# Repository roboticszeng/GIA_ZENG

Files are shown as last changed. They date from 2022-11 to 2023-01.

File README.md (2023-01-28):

# GIA_ZENG开发文档

| 更新时间  | 版本号 | 更新内容 | 负责人 |
| --- | --- | --- | --- |
| 2023.1.21 | V0.2 | 初始化文档 | RoboticsZeng |

## 1.结构设计

==Reserve==

## 2.硬件设计

==Reserve==

## 3.软件设计

GIA_ZENG软件层按照应用功能主要分为以下几部分：FOC控制、自标定、数据存储和对外通讯，其中包含相关驱动的开发和数值解算。下面分别详细说明。

### 3.1 FOC控制

FOC控制是BLDC驱动的核心功能，其流程如下图所示：

==缺一张网图==

上述功能主要依赖以下算法：SVPWM计算、位置速度估计、电流估计、PI控制器、滤波器。另外需要相应的硬件驱动开发。

#### 3.1.1 SVPWM计算

GIA_ZENG采用的是有感FOC，故电角度为已知量，首先进行反park变换：
$$
U_{\alpha} = U_d\cos q_e + U_q\sin q_e
$$

$$
U_{\beta}=U_d\sin q_e + U_q\cos q_e
$$

==Reserve==

#### 3.1.2 位置速度估计

AS5600可以直接获得12位绝对位置，通过单位转换函数`convert_pulse_to_angle`转换为角度，单位rad。

速度采用M法进行估计，如下式：
$$
v=(p-p_{prev})/T
$$
其中，$p$为当前时刻位置，单位rad；

$p_{prev}$为上一时刻位置，单位rad；

$T$为编码器采样时间，单位s；

$v$为估计速度值，单位rad/s。

#### 3.1.3 电流估计

INA240可以直接通过12位ADC获得两相电压值，进行校正后再通过单位转换函数`convert_pulse_to_current`转换为电流，单位A。进一步计算q轴和d轴的方式如下：

（1）Clarke变换到$I_{\alpha}, I_{\beta}$
$$
I_{\alpha}=I_a
$$

$$
I_{\beta} = \frac{\sqrt{3}}{3}(I_a+2I_b)
$$

（2）Park变换到$I_q,I_d$
$$
I_d=I_{\alpha}\cos q_e + I_{\beta}\sin q_e
$$

$$
I_q=-I_{\alpha}\sin q_e + I_{\beta}\cos q_e
$$

#### 3.1.3 PI控制器

本方案采用抗积分饱和的离散PID控制器，其逻辑如下：

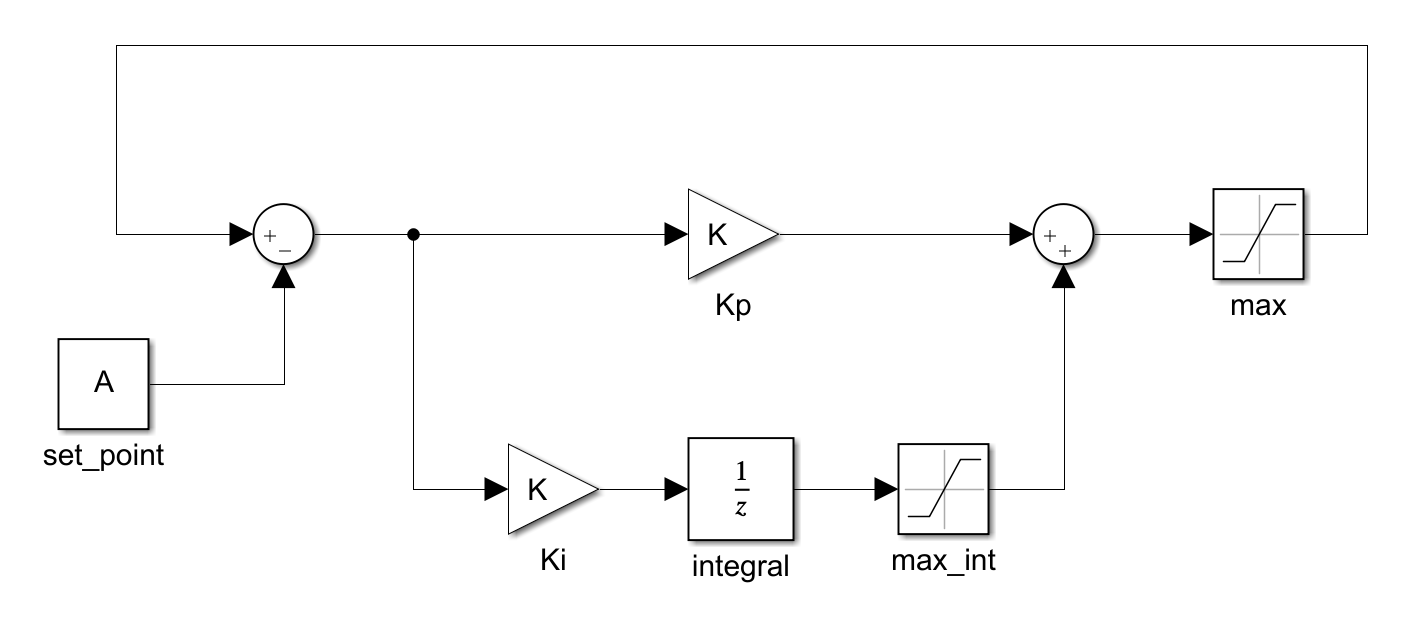
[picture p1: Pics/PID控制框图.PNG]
PID控制框图


PI控制器算法逻辑不再赘述。

#### 3.1.4 低通滤波器

本方案对速度、q轴电流和d轴电流计算时采用了一阶低通滤波器，其s域表达为：
$$
G(s) = \frac{1}{\frac{s}{2\pi f_c} + 1}
$$
其中，$f_c$为数字截止频率。

向后差分到z域再写成差分方程：
$$
y(n)=\frac{RC}{T_s+RC}y(n-1)+\frac{T_s}{T_s+RC}x(n)
$$
其中，$T_s$为采样时间，$RC=\frac{1}{2\pi f_c}$

#### ==3.1.5 展望==

- 加入数字截止频率到模拟截止频率的转换
- 改为二阶butterworth滤波器
- 向后差分改成tustin

### 3.2 电角度&ADC校正

本方案对电角度和ADC偏置量采用了自动和手动校正的方法，具体步骤如下：

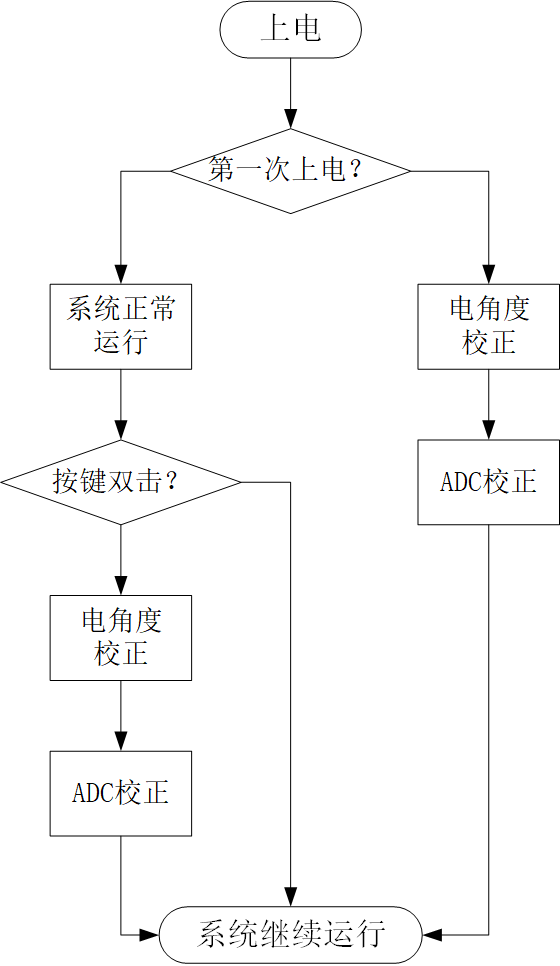
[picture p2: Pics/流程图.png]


#### 3.2.1 电角度校正

设置开环SVPWM控制如下：

| $U_q$ | $U_d$ | $q_e$ |
| ----- | ----- | ----- |
| 0.5 | 0.0 | 0.0 |

注意此处的$U_q,U_d$为相对供电电压的相对值，取值范围$[-1,1]$

循环设置N次上述电角度对正，同时通过编码器读取当前位置，求平均值得到校正的电角度，作为单位转换函数`compute_position_elec`的配置项。

#### 3.2.2 ADC校正

设置控制模式为MODE_NO确保驱动器未使能，当前电流为零，循环采集N次此时刻的ADC值，求平均值得到校正的ADC偏置量，在ADC采样时作为输入。注意由于INA240芯片易损坏，此处需要手动check偏置量是否正确，即观察偏置值是否在2048附近。

#### ==3.2.3 展望==

- 校正时需要加入合理的小灯闪烁来指示正在校正
- 加入ADC求偏置的单位转换函数，不要直接写在ADC采样内

### 3.3 CAN通讯

本方案当前仅采用了CAN通讯与其他MCU或上位机交互数据，同时USART用于打印调试信息。文档中仅介绍CAN通讯。CAN读写均采用扩展数据帧形式，数据形式定义为PDO（循环上报）和SDO（根据指令上报）。

#### 3.3.1 CAN读取

（1）PDO

PDO数据循环上报，无需读取，其数据格式为：

| data[0] | data[1] | data[2] | data[3] | data[4] | data[5] | data[6] | data[7] |
| --- | --- | --- | --- | --- | --- | --- | --- |
| mode_h  | mode_l  | actual_pos_h | actual_pos_l | actual_vel_h | actual_vel_l | actual_cur_h | actual_cur_l |

其中，\*\_h和\*\_l分别为*的高八位和低八位。其具体数值和单位转换的方式参考附录。

（2）SDO

读取数据格式为：

| data[0] | data[1] | data[2] | data[3] | data[4] | data[5] | data[6] | data[7] |
| --- | --- | --- | --- | --- | --- | --- | --- |
| 0x56 | id* | Reserve | Reserve | Reserve | Reserve | 0x0d**  | 0x0a |

*：id为当前关节的id号，默认为0x00

**：推荐的值，当前程序还没有设置check这一位

软件在收到数据头为0x56的CAN数据包后开始解析，将当前CAN地址下的SDO数据返回。

#### 3.3.2 CAN写入

PDO和SDO的写入逻辑相同，均是在软件内重构了CAN_RX中断，读取的数据格式为：

| data[0] | data[1] | data[2] | data[3] | data[4] | data[5] | data[6] | data[7] |
| --- | --- | --- | --- | --- | --- | --- | --- |
| 0x55 | id | data_h  | data_l  | Reserve | Reserve | 0x0d | 0x0a |

软件在收到数据头为0x55的CAN数据包后开始解析，将当前CAN地址下的PDO或SDO数据写入控制器。

#### 3.3.3 PDO/SDO转换

上位机向控制器发送PDO/SDO后，还需要将这一`uint16_t`类型的标准参数转换为实际使用的配置值或控制目标值，这一逻辑较复杂，具体分为以下几种情况：

（1）收到的数据是PDO：MODE_OF_OPERATION, TARGET_POSITION, TARGET_VELOCITY, TARGET_CURRENT

- STEP1: 解析地址，将收到的数据存入PDO结构体的指定成员中。
- STEP2: 由下式转化为State结构体的指定成员。

$$
State=256*PDO_h+PDO_l
$$

- STEP3: FOC三环控制的定时器中断中只调用State成员的变量进行实时控制，而不考虑PDO的问题

（2）收到的数据是除上述之外的PDO：无意义，不作响应

（3）收到的数据是SDO，但不是`SDO->ID`或`SDO->SAVE_FLASH`

- STEP1: 解析地址，将收到的数据存入`SDO->SDO_ID`
- STEP2: 调用函数`para_init`初始化所有config参数

`para_init`函数包括：

#### ==3.3.4 展望==

- CAN回传PDO时只用了一个邮箱传输了部分数据，这是由于邮箱容易被占用阻塞，后续应解决这一问题

### 3.4 配置读写和存储

配置读写和存储的逻辑较为复杂，具体的涉及到以下几个方面：CAN通讯收到的PDO/SDO数据转换为实际使用的配置值或控制目标值；上电时的配置读取逻辑；基于内部FLASH的数据存储逻辑。下面分别叙述。

#### 3.4.1 PDO/SDO的转换

#### 3.4.2 配置参数读取

#### 3.4.3 配置参数存储

### 3.5 依赖硬件的说明

本文档中对硬件驱动的详细逻辑不再赘述，仅给出依赖硬件驱动的说明。

STM32CUBEMX引脚总览：

| 引脚 | 名称 | 备注 |
| ---- | --- | --- |
| PA0  | ADC1_IN0  | |
| PA1  | ADC1_IN1  | |
| PA2  | USART2_TX | |
| PA3  | USART2_RX | |
| PA4  | SEN_DIR | 编码器方向定义 |
| PA5  | KEY | 按键输入，软件暂未实现 |
| PA8  | TIM1_CH1  | PWM-U相输出 |
| PA9  | TIM1_CH2  | PWM-V相输出 |
| PA10 | TIM1_CH3  | PWM-W相输出 |
| PA11 | CAN_RX | |
| PA12 | CAN_TX | |
| PB5  | SENS_OUT  | 编码器电压输出（当前版本不用） |
| PB6  | I2C1_SCL  | 编码器I2C通信 |
| PB7  | I2C1_SDA  | 编码器I2C通信 |
| PC13 | LED | |

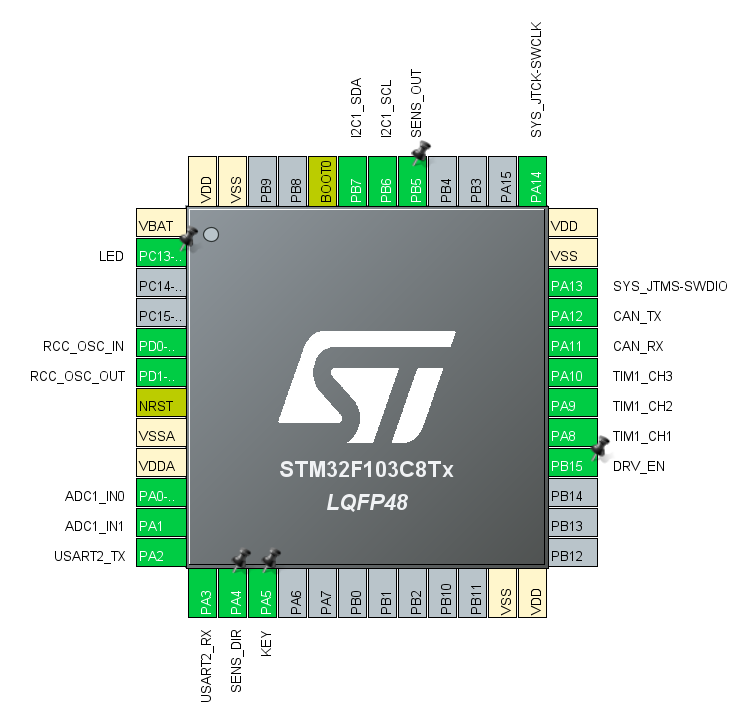
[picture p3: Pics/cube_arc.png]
cube_arc


#### 3.5.1 定时器中断

本方案中采用了四个定时器中断如下：

| 定时器 | 分频值PSC | 重装值ARR | 周期T | 频率f | 功能简介 |
| --- | --- | --- | --- | --- | --- |
| TIM1 | 2-1 | 1500-1 | 41.67us | 24kHz | 生成PWM波&电流采样&电流滤波 |
| TIM2 | 300-1 | 240-1 | 1ms | 1000Hz | 编码器采样&速度估计滤波&CAN上报 |
| TIM3 | 160-1 | 72-1 | 160us | 6.25kHz  | 计算SVPWM&电流环PI控制 |
| TIM4 | 160-1 | 144-1 | 320us | 3.125kHz | 位置环&速度环PI控制 |

注：定时器分频、重装值和周期/频率的转换关系如下：

公式：
$$
T=(ARR+1)*(PSC+1)/f_{ck}
$$

$$
f=\frac{1}{T}
$$

$f_{ck}$为主频，单位Hz。对于STM32F103C8T6，$f_{ck}=72\times10^6$Hz；$T$单位为s。

#### 3.5.2 I2C通讯

编码器AS5600通过I2C与主控制器通信，模式Fast Mode，通信速率400kHz

#### 3.5.3 ADC读取

主控制器通过ADC1双通道IN0和IN1读取两片INA240的电压，采用DMA方式。

#### 3.5.4 按键外部中断

设置PA5引脚为GPIO_EXTI5，EXTI_line[9:5] interrupt中断优先级5，注意此处必须设置System Ticker Timer优先级小于5，否则可能会在中断处卡住。

本方案对按键中断设计了单击、双击、长按三个事件，其功能如下：

| 事件 | 功能 |
| --- | --- |
| 单击 | 指示灯电平翻转 |
| 双击 | 手动电角度&ADC校正  |
| 长按（>1s） | 存储数据到内部FLASH |

#### 3.5.5 CAN通讯

#### 3.5.6 内部FLASH

## 4.附录

### 4.1 单位转换

### 4.2 通讯协议详解

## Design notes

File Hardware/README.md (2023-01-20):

# GIA硬件板卡设计

## 1.总览

### 1.1 IC及原理图设计

- STM32F103C8T6：

最小板参考已实现的方式设计，不要低频晶振

- L6234PD（补购10片）

参考已实现的方式设计，EN预留IO，注意务必理解、实现保护地和地

- AS5600

STM32预留可编程电阻和方向口的IO

- INA240A2*2（补购10片）

用嘉立创的0.01R电阻

- TPS54331（补购10片）

复用灯哥开源的电路

- ASM1117-3.3

参考验证版的选型和电路

- TJA1040T

预留120R终端电阻接口，但是不焊（调试时用上位机的终端电阻）(**明天开始先调CAN和flash算了。。。。**)

- 其他

LED灯查下匹配的电阻，不要太亮也不要太暗

### 1.2 接口（全部放在反面）

- [x] UVW：2.54-3P螺钉式接线端子
- [x] DCBUS：2.54-2P插拔式接线端子弯插
- [x] CAN***2**：SH1.0-2P贴片 / PH2.0-2P弯插
- [x] I2C：预留一路SH1.0-4P贴片（注意若SWD为SH1.0，务必保证和SWD的VCC/GND一致）
- [x] USART：SH1.0-3P贴片 / PH2.0-3P弯插
- [x] SWD：SH1.0-4P贴片 / PH2.0-4P弯插
- [x] LED：电源灯（蓝灯）、PC13灯（DEBUG绿灯）、编码器方向灯（红灯常灭）三个灯PCB上尽量放在一起
- [ ] INA240-IO引脚留出，手焊短接，尽量方便手焊的位置
- [ ] PC13在边缘留一个焊盘用于DEBUG
- [ ] 留圆盘小按键用于重置STM32

### 1.3 PCB Layout注意事项

- [ ] 晶振不要放在边缘
- [ ] AS5600居中
- [ ] UVW端子观察电机布置
- [ ] 所有接口都贴在反面
- [ ] INA240贴在反面
- [ ] 灯都贴在反面
- [ ] 某两个孔中间角度连电机端子，依次均布接口不要超过电机端子的正负90deg
- [ ] 以后可以把编码器和控制器分开做异形PCB，想想都很酷炫
- [ ] PCB板直径68，孔距44，4个孔，思考下以后怎么安装

### 1.4 原理图设计注意事项

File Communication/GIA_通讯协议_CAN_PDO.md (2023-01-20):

# GIA\_通讯协议\_CAN_PDO

8位数据，数据头55，数据尾0d0a

## Bit[0]: 数据头0x55

## Bit[1]: 关节号Joint Number

| 取值 | 说明 |
| ---- | --- |
| 0xd0 | 关节1 |
| 0xd1 | 关节2 |
| 0xd2 | 关节3 |
| 0xd3 | 关节4 |
| 0xd4 | 关节5 |
| 0xd5 | 关节6 |
| 0xd6 | 关节7 |
| else | Error, returnBit[0] = 1 |

## Bit[2~3]: PDO值

### 1. ActualPosition==(ADDRESS = 0x3082)==

```
Bit[2] = _get_high_byte_uint(oPdo->actual_position)
Bit[3] = _get_low_byte_uint(oPdo->actual_position)
```

actual_position 取值范围 0~4096，直接由函数`as5600_get_raw_angle(oEncoder, &actual_position)`采集得到
$$
q=(p-p_0)\frac{2\pi}{4096}
$$

$$
p=\frac{4096}{2\pi}q+p_0
$$

==未实现的：==

```
#define _get_high_byte_uint(data) (data & 0xff00) //取无符号整型数据的高8位
#define _get_low_byte_uint(data) (data & 0x00ff) //取无符号整型数据的低8位
```

### 2. ActualVelocity==(ADDRESS = 0x3085)==

```
Bit[2] = _get_high_byte_int(oPdo->actual_velocity)
Bit[3] = _get_low_byte_int(oPdo->actual_velocity)
```

actual_velocity取值范围±20480（电机额定转速300rpm），由函数`get_velocity`计算得到
$$
\dot q=(p-32768)\frac{2\pi}{4096}
$$

$$
p=\frac{4096}{2\pi}q+32768
$$

==未实现的：==

```
#define _get_high_byte_int(data) ((data + 0x8000) & 0xff00)
#define _get_low_byte_int(data) ((data + 0x8000) & 0x00ff)
```

==未实现的：==

```
get_velocity 
```

### 3. Actual Current-Q==(ADDRESS = 0x330E)==

```
Bit[2] = _get_high_byte_uint(oPdo->actual_current_q)
Bit[3] = _get_low_byte_uint(oPdo->actual_current_q)
```

actual_current_q 取值范围0~4096，由函数`convert_current_to_pulse`计算得到

计算方法，已知电流采样时：
$$
I=\frac{p-2048}{K*R}*\frac{3.3}{4096}
$$
那么交换顺序：
$$
p=K*R*I*\frac{4096}{3.3}+2048
$$
其中，$K$为放大系数50，$R$为采样电阻0.01Ω，4096为ADC分辨率

==未实现的：==

```
convert_current_to_pulse
```

### 4. Actual Current-D==(ADDRESS = 0x330D)==

```
Bit[2] = _get_high_byte_uint(oPdo->actual_current_d)
Bit[3] = _get_low_byte_uint(oPdo->actual_current_d)
```

和3.完全一样

### 5. Mode Of Operation Display==(ADDRESS=0x3081)==

```
Bit[2] = 0x00;
Bit[3] = oPdo->mode;
```

mode取值范围0x00,0x08,0x09,0x0a

### 6. Following Error==(ADDRESS=0x3084)==

```
switch (oPdo->mode){
	case MODE_CSP:
	oPdo->following_error = oPdo->target_position - oPdo->actual_position;
	
	break;
	case MODE_CSV:
	oPdo->following_error = oPdo->target_velocity - oPdo->actual_position;
	
	break;
	case MODE_CST:
	oPdo->following_error = oPdo->target_current_q - oPdo->actual_current_q;
	
	break;
	otherwise:
	oPdo->following_error = 0;
	break;
}
// 上面的计算也可以放在三环里算

Bit[2] = _get_high_byte_int(oPdo->following_error)
Bit[3] = _get_low_byte_int(oPdo->following_error)
```

## Bit[4]~Bit[5]: 目标值TargetValue = Bit[4] * 0x100 + Bit[5]

### 1. Bit[2] == 0x08||0x09||0x0a

| Bit[2] Value | Bit[4] 含义  | 单位 | 取值范围 | 转换关系 |
| --- | --- | --- | --- | --- |
| 0x08 | 目标位置 | count | 0~4096 | TargetPos = Bit[2] |
| 0x09 | 目标速度 | count/s | 0~40960 | TargetVel = Bit[2] - 20480 |
| 0x0a | 目标电流 | count_i | 0~4096 | TargetCur = Bit[2] - 2048  |
| 0x08\|\|0x09\|\|0x0a | 超出取值范围 | | returnBit[2]=1 | |

示例：

Bit[2] = 0x08, TargetValue = 2048 ==> 目标位置为2048count

Bit[2] = 0x09, TargetValue  = 0 ==> 目标速度为-20480rad/s

Bit[2] = 0x0a, TargetValue  = 0 ==> 目标电流为-2048count_i

提供两个常数：

Const_count_to_pos = (2*PI)/4096 rad/count

Const_count_to_cur = 6.6/4096 A/count (INA240A2_50V/V + 0.01R)

### 2. Bit[2] == 0x10 || 0x20

上报16Bit配置参数，上报数据根据TargetValue的取值不同，输出格式如下

| Target Value | 数据位 | 说明 | 单位 | 取值范围 |
| --- | --- | --- | --- | --- |
| / | 0 | 数据头:0x55 | | |
| | 1 | Joint Number:0xd0~0xd6 | | |
| 0x3000:Actual State | 2.3 | Actual Position | | |
| | 4.5 | Actual Velocity | | |
| | 6.7 | Actual Current-Q | | |
| | 8.9 | Actual Current-D | | |
| | 10.11  | Mode of Operation Display | Next Ver | |
| | 12.13  | Following Error | Next Ver | |
| 0x3080:Target State | 2.3 | 最近一次Target Position | | |
| | 4.5 | 最近一次Target Velocity | | |
| | 6.7 | 最近一次Target Current-Q  | | |
| | 8.9 | 最近一次Velocity Offset | Next Ver | |
| | 10.11  | 最近一次Current Offset | Next Ver | |
| | 12.13  | 最近一次Mode Of Operation | Next Ver | |
| 0x3300:Pos Demand | 2.3 | Position Demand Value | | |
| | 4.5 | Limited Position | | |
| | 6.7 | Position Loop Effort | Next Ver | |
| 0x3303:Vel Demand | 2.3 | Velocity Demand Value | | |
| | 4.5 | Limited Velocity | | |
| | 6.7 | Velocity Loop Effort | Next Ver | |
| 0x3309:Cur-Phase Actual | 2.3 | Actual Current A-Phase | | |
| | 4.5 | Actual Current B-Phase | | |
| 0x330d:Cur-Q Demand | 2.3 | Current-Q Demand Value | | |
| | 4.5 | Limited Current-D | | |
| | 6.7 | Current-Q Loop Effort | Next Ver | |
| 0x330e:Cur-D Demand | 2.3 | Current-D Demand Value | Next Ver | |
| | 4.5 | \ | | |
| | 6.7 | Current-D Loop Effort | | |
| **0x3506:Pos Loop Para Std** | 6.7 | KP_P_STD | Next Ver | |
| | 8.9 | KI_P_STD | | |
| | 10.11  | KD_P_STD | | |
| **0x3507:Vel Loop Para Std** | 6.7 | KP_V_STD | Next Ver | |
| | 8.9 | KI_V_STD | | |
| | 10.11  | KD_V_STD | | |
| **0x3508:Cur-Q Loop Para Std** | 6.7 | KP_Q_STD | Next Ver | |
| | 8.9 | KI_Q_STD | | |
| | 10.11  | KD_Q_STD | | |
| **0x3509:Cur-D Loop Para Std** | 6.7 | KP_D_STD | Next Ver | |
| | 8.9 | KI_D_STD | | |
| | 10.11  | KD_D_STD | | |
| **0x3516:Pos Loop Para Per** | 6.7 | KP_P_PER | 0~65535  | 0.001 |
| | 8.9 | KI_P_PER | | |
| | 10.11  | KD_P_PER | | |
| **0x3517:Vel Loop Para Per** | 6.7 | KP_V_PER | | |
| | 8.9 | KI_V_PER | | |
| | 10.11  | KD_V_PER | | |
| **0x3518:Cur-Q Loop Para Per** | 6.7 | KP_Q_PER | | |
| | 8.9 | KI_Q_PER | | |
| | 10.11  | KD_Q_PER | | |
| **0x3519:Cur-D Loop Para Per** | 6.7 | KP_D_PER | | |
| | 8.9 | KI_D_PER | | |
| | 10.11  | KD_D_PER | | |
| **0x3510:Pos Limit** | 6.7 | 位置环上限幅 | count | |
| | 8.9 | 位置环下限幅 | count | |
| **0x3512:Vel Limit** | 6.7 | 速度环上限幅 | count/s  | |
| | 8.9 | 速度环下限幅 | count/s  | 上限取反 |
| **0x3514:Cur-Q Limit** | 6.7 | 电流环d轴上限幅 | count_i  | |
| | 8.9 | 电流环d轴下限幅 | count_i  | 上限取反 |
| **0x3515:Cur-D Limit** | 6.7 | 电流环q轴上限幅 | count_i  | |
| | 8.9 | 电流环q轴下限幅 | count_i  | 上限取反 |
| **0x3500:Motor Const** | 6.7 | 极对数：14 | | |
| | 8.9 | 供电电压：24 | V | |
| **0x3501:Encoder Const** | 6.7 | 线数：4096 | | 0~65535 |
| | 8.9 | 编码器偏置 | | Next Ver |
| | 10.11  | 电角度偏置 | | 待完成 |
| **0x3502:ADC Const** | 6.7 | 线数：4096 | | 0~65535 |
| | 8.9 | ADC_0偏置 | count_i  | -2048~2048 |
| | 10.11  | ADC_1偏置 | count_i  | -2048~2048 |
| **0x3503:Mechanical Const** | 6.7 | 电流和位置的方向：0(neg)  | | 0~1 |
| **0x3505:Cur-Sample Const** | 6.7 | 采样电阻：10 | mΩ | 0~65535 |
| | 8.9 | 增益系数：50 | V/V | 0~65535 |
| | 10.11  | MCU电压：3300 | mV | 0~65535 |
| / | 14 | 数据尾:0x0d | | |
| / | 15 | 数据尾:0x0a | | |

若Bit[2] = 0x20，则为写入模式，其取值同上表，只取到**加粗**的数值。

示例：

Bit[2] = 0x10, TargetValue = 0x3502：读ADC常数，按上表格式输出

Bit[2] = 0x20, TargetValue = 0x3502：写ADC常数，写入格式为Bit[6\~7]计算线数，Bit[8\~9]计算ADC_0偏置，Bit[10\~11]计算ADC_1偏置，以此类推。

+ 滤波参数当前版本暂未写入

### 4. Bit[2] == 0x12 || 0x13 || 0x14

Reserve.

## Bit [6~11]: 配置值

仅当Bit[2] == 0x20 时生效，取值意义参照上表。

## Bit [12~13]: Reserve

## Bit [14~15]: 0x0d 0x0a 数据尾

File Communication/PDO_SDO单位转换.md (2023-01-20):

# PDO_SDO单位转换

## PDO

### 1.PDO_MODE_OF_OPERATION

| ADDRESS | RANGE |
| --- | ----- |
| 0x3001  | \ |

Formula:
$$
PDO=In_l
$$

```
PDO_MODE_OF_OPERATION = Rxdata[3];
```

Example:

```
Rxdata = {0x55, 0x00, 0x00, 0x0a, 0x00, 0x00, 0x0d, 0x0a};
PDO_MODE_OF_OPERATION = 0x0a;
```

### 2.PDO_TARGET_POSITION

| ADDRESS | RANGE  |
| --- | --- |
| 0x3002  | 0~4096 |

Formula:
$$
PDO=In_h * 256 + In_l
$$

```
temp = _convert_8bit_to_16bit(Rxdata[2], Rxdata[3]);
if(_check_range(temp, oSdo->SDO_TARGET_POSITION_LB, oSdo->SDO_TARGET_POSITION_UB) == 1)
{
	oPdo->PDO_TARGET_POSITION = temp;
}
```

### 3.PDO_TARGET_VELOCITY

| ADDRESS | RANGE |
| --- | --- |
| 0x3003  | -32768~32767 |

Formula:
$$
PDO=In_h*256+In_l
$$

### 4.PDO_TARGET_CURRENT_Q

## SDO

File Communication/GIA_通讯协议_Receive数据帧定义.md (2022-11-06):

# GIA\_通讯协议\_Receive数据帧定义

16位数据，数据头55，数据尾0d0a

## Bit[0]: 数据头0x55

## Bit[1]: 关节号Joint Number

| 取值 | 说明 |
| ---- | --- |
| 0xd0 | 关节1 |
| 0xd1 | 关节2 |
| 0xd2 | 关节3 |
| 0xd3 | 关节4 |
| 0xd4 | 关节5 |
| 0xd5 | 关节6 |
| 0xd6 | 关节7 |
| else | Error, returnBit[0] = 1 |

## Bit[2]: 控制类型Type

| 取值 | 模式 | 说明 |
| ---- | --- | --- |
| 0x00 | No Mode | |
| 0x01 | PP Mode | Next Ver |
| 0x08 | CSP Mode | |
| 0x09 | CSV Mode | |
| 0x0a | CST Mode | |
| 0x10 | Read Mode | 读取配置参数 |
| 0x12 | Internal CSP Mode | Next Ver |
| 0x13 | Internal CSV Mode | Next Ver |
| 0x14 | Internal CST Mode | Next Ver |
| 0x20 | Write Mode | 写入配置参数 |
| 0x21 | Electric Angle Calibrate Mode | 电角度校正模式, 待完成 |
| 0x22 | Encoder Calibrate Mode | 编码器校正模式, Next Ver |
| 0x23 | ADC Calibrate Mode | ADC校正模式, 待完成 |
| 0xff | Initial Mode | 初始化模式, 待完成 |
| else | Error, returnBit[1] = 1 | |

## Bit[3]: Reserve

## Bit[4]~Bit[5]: 目标值TargetValue = Bit[4] * 0x100 + Bit[5]

### 1. Bit[2] == 0x08||0x09||0x0a

| Bit[2] Value | Bit[4] 含义  | 单位 | 取值范围 | 转换关系 |
| --- | --- | --- | --- | --- |
| 0x08 | 目标位置 | count | 0~4096 | TargetPos = Bit[2] |
| 0x09 | 目标速度 | count/s | 0~40960 | TargetVel = Bit[2] - 20480 |
| 0x0a | 目标电流 | count_i | 0~4096 | TargetCur = Bit[2] - 2048  |
| 0x08\|\|0x09\|\|0x0a | 超出取值范围 | | returnBit[2]=1 | |

示例：

Bit[2] = 0x08, TargetValue = 2048 ==> 目标位置为2048count

Bit[2] = 0x09, TargetValue  = 0 ==> 目标速度为-20480rad/s

Bit[2] = 0x0a, TargetValue  = 0 ==> 目标电流为-2048count_i

提供两个常数：

Const_count_to_pos = (2*PI)/4096 rad/count

Const_count_to_cur = 6.6/4096 A/count (INA240A2_50V/V + 0.01R)

### 2. Bit[2] == 0x10 || 0x20

上报16Bit配置参数，上报数据根据TargetValue的取值不同，输出格式如下

| Target Value | 数据位 | 说明 | 单位 | 取值范围 |
| --- | --- | --- | --- | --- |
| / | 0 | 数据头:0x55 | | |
| | 1 | Joint Number:0xd0~0xd6 | | |
| 0x3000:Actual State | 2.3 | Actual Position | | |
| | 4.5 | Actual Velocity | | |
| | 6.7 | Actual Current-Q | | |
| | 8.9 | Actual Current-D | | |
| | 10.11  | Mode of Operation Display | Next Ver | |
| | 12.13  | Following Error | Next Ver | |
| 0x3080:Target State | 2.3 | 最近一次Target Position | | |
| | 4.5 | 最近一次Target Velocity | | |
| | 6.7 | 最近一次Target Current-Q  | | |
| | 8.9 | 最近一次Velocity Offset | Next Ver | |
| | 10.11  | 最近一次Current Offset | Next Ver | |
| | 12.13  | 最近一次Mode Of Operation | Next Ver | |
| 0x3300:Pos Demand | 2.3 | Position Demand Value | | |
| | 4.5 | Limited Position | | |
| | 6.7 | Position Loop Effort | Next Ver | |
| 0x3303:Vel Demand | 2.3 | Velocity Demand Value | | |
| | 4.5 | Limited Velocity | | |
| | 6.7 | Velocity Loop Effort | Next Ver | |
| 0x3309:Cur-Phase Actual | 2.3 | Actual Current A-Phase | | |
| | 4.5 | Actual Current B-Phase | | |
| 0x330d:Cur-Q Demand | 2.3 | Current-Q Demand Value | | |
| | 4.5 | Limited Current-D | | |
| | 6.7 | Current-Q Loop Effort | Next Ver | |
| 0x330e:Cur-D Demand | 2.3 | Current-D Demand Value | Next Ver | |
| | 4.5 | \ | | |
| | 6.7 | Current-D Loop Effort | | |
| **0x3506:Pos Loop Para Std** | 6.7 | KP_P_STD | Next Ver | |
| | 8.9 | KI_P_STD | | |
| | 10.11  | KD_P_STD | | |
| **0x3507:Vel Loop Para Std** | 6.7 | KP_V_STD | Next Ver | |
| | 8.9 | KI_V_STD | | |
| | 10.11  | KD_V_STD | | |
| **0x3508:Cur-Q Loop Para Std** | 6.7 | KP_Q_STD | Next Ver | |
| | 8.9 | KI_Q_STD | | |
| | 10.11  | KD_Q_STD | | |
| **0x3509:Cur-D Loop Para Std** | 6.7 | KP_D_STD | Next Ver | |
| | 8.9 | KI_D_STD | | |
| | 10.11  | KD_D_STD | | |
| **0x3516:Pos Loop Para Per** | 6.7 | KP_P_PER | 0~65535  | 0.001 |
| | 8.9 | KI_P_PER | | |
| | 10.11  | KD_P_PER | | |
| **0x3517:Vel Loop Para Per** | 6.7 | KP_V_PER | | |
| | 8.9 | KI_V_PER | | |
| | 10.11  | KD_V_PER | | |
| **0x3518:Cur-Q Loop Para Per** | 6.7 | KP_Q_PER | | |
| | 8.9 | KI_Q_PER | | |
| | 10.11  | KD_Q_PER | | |
| **0x3519:Cur-D Loop Para Per** | 6.7 | KP_D_PER | | |
| | 8.9 | KI_D_PER | | |
| | 10.11  | KD_D_PER | | |
| **0x3510:Pos Limit** | 6.7 | 位置环上限幅 | count | |
| | 8.9 | 位置环下限幅 | count | |
| **0x3512:Vel Limit** | 6.7 | 速度环上限幅 | count/s  | |
| | 8.9 | 速度环下限幅 | count/s  | 上限取反 |
| **0x3514:Cur-Q Limit** | 6.7 | 电流环d轴上限幅 | count_i  | |
| | 8.9 | 电流环d轴下限幅 | count_i  | 上限取反 |
| **0x3515:Cur-D Limit** | 6.7 | 电流环q轴上限幅 | count_i  | |
| | 8.9 | 电流环q轴下限幅 | count_i  | 上限取反 |
| **0x3500:Motor Const** | 6.7 | 极对数：14 | | |
| | 8.9 | 供电电压：24 | V | |
| **0x3501:Encoder Const** | 6.7 | 线数：4096 | | 0~65535 |
| | 8.9 | 编码器偏置 | | Next Ver |
| | 10.11  | 电角度偏置 | | 待完成 |
| **0x3502:ADC Const** | 6.7 | 线数：4096 | | 0~65535 |
| | 8.9 | ADC_0偏置 | count_i  | -2048~2048 |
| | 10.11  | ADC_1偏置 | count_i  | -2048~2048 |
| **0x3503:Mechanical Const** | 6.7 | 电流和位置的方向：0(neg)  | | 0~1 |
| **0x3505:Cur-Sample Const** | 6.7 | 采样电阻：10 | mΩ | 0~65535 |
| | 8.9 | 增益系数：50 | V/V | 0~65535 |
| | 10.11  | MCU电压：3300 | mV | 0~65535 |
| / | 14 | 数据尾:0x0d | | |
| / | 15 | 数据尾:0x0a | | |

若Bit[2] = 0x20，则为写入模式，其取值同上表，只取到**加粗**的数值。

示例：

Bit[2] = 0x10, TargetValue = 0x3502：读ADC常数，按上表格式输出

Bit[2] = 0x20, TargetValue = 0x3502：写ADC常数，写入格式为Bit[6\~7]计算线数，Bit[8\~9]计算ADC_0偏置，Bit[10\~11]计算ADC_1偏置，以此类推。

+ 滤波参数当前版本暂未写入

### 4. Bit[2] == 0x12 || 0x13 || 0x14

Reserve.

## Bit [6~11]: 配置值

仅当Bit[2] == 0x20 时生效，取值意义参照上表。

## Bit [12~13]: Reserve

## Bit [14~15]: 0x0d 0x0a 数据尾

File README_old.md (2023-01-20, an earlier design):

# 通用一体化关节项目GIA_Zeng

| 修订日期 | 修订内容 | 修订版本  |
| --- | --- | --- |
| 2022/10/30 | 新建文档 | Beta1.0.0 |

## 1.结构设计

## 2.硬件设计

+ MCU-STM32F103C8T6：

BOOT位设置：

LED控制灯：

+ 编码器：

AS5600-I2C读取

方向设置

+ 电源：

24V-5V

匹配电阻：

5V-3V3

+ 电流采样：

INA240A3PWR 100V/V 0.01R电阻

电流采样范围：-1.65~1.65A，匹配电机额定电流0.75A

下限 (0-1.65)/0.01/100=-1.65A

上限 (3.3-1.65)/0.01/100=1.65A

+ 驱动：

L6234D，功率偏大，下一版可以考虑换DRV8313？

+ 硬件接口：

贴片式接线端子

- 电机GB6010信息（厂商提供，待测）

[淘宝链接](https://item.taobao.com/item.htm?spm=a1z09.2.0.0.7d002e8dyVimGY&id=639378697535&_u=c239sn30f500)

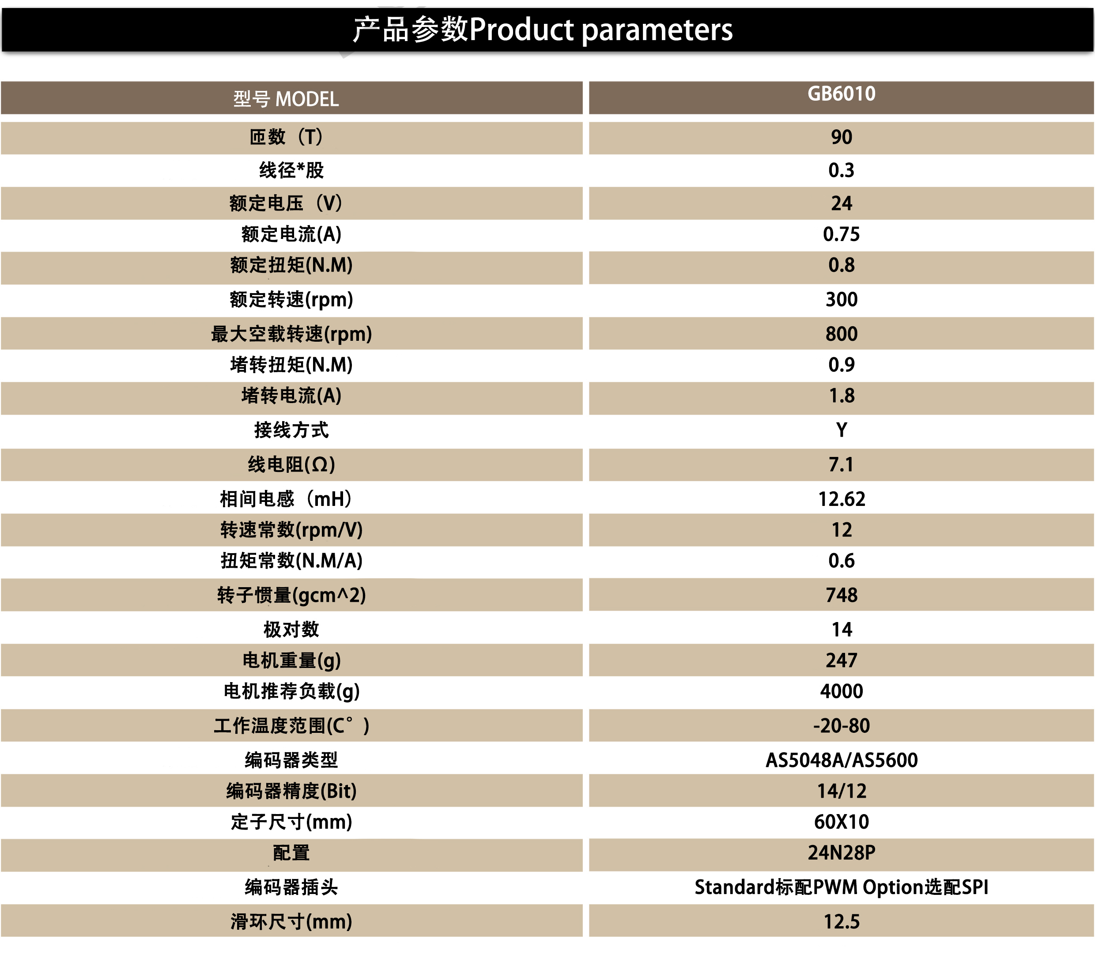
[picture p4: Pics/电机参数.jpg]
电机参数


主要的问题：

- 如何测定额定电流和额定扭矩？
- 转速常数12rpm/V,也即24V时转速应为30rad/s，但实际上似乎没这么大？
- 扭矩常数0.6，额定力矩和额定电流对不上
- 

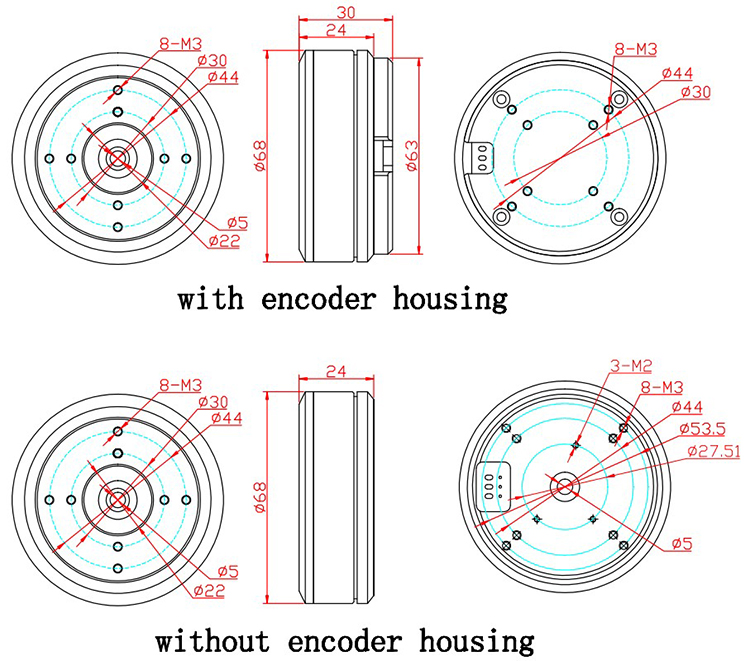
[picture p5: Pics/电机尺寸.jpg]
电机尺寸


## 3.软件设计

+ STM32CUBEMX引脚总览：

| 引脚 | 名称 | 备注 |
| ---- | --- | --- |
| PA0  | ADC1_IN0  | |
| PA1  | ADC1_IN1  | |
| PA2  | USART2_TX | |
| PA3  | USART2_RX | |
| PA4  | SEN_DIR | 编码器方向定义 |
| PA5  | KEY | ==按键输入，软件暂未实现== |
| PA8  | TIM1_CH1  | PWM-U相输出 |
| PA9  | TIM1_CH2  | PWM-V相输出 |
| PA10 | TIM1_CH3  | PWM-W相输出 |
| PA11 | CAN_RX | |
| PA12 | CAN_TX | |
| PB5  | SENS_OUT  | 编码器电压输出（当前版本不用） |
| PB6  | I2C1_SCL  | 编码器I2C通信 |
| PB7  | I2C1_SDA  | 编码器I2C通信 |
| PC13 | LED | |

+ STM32CUBEMX-Clock总览：

cube_arc

+ NVIC：==待更新==

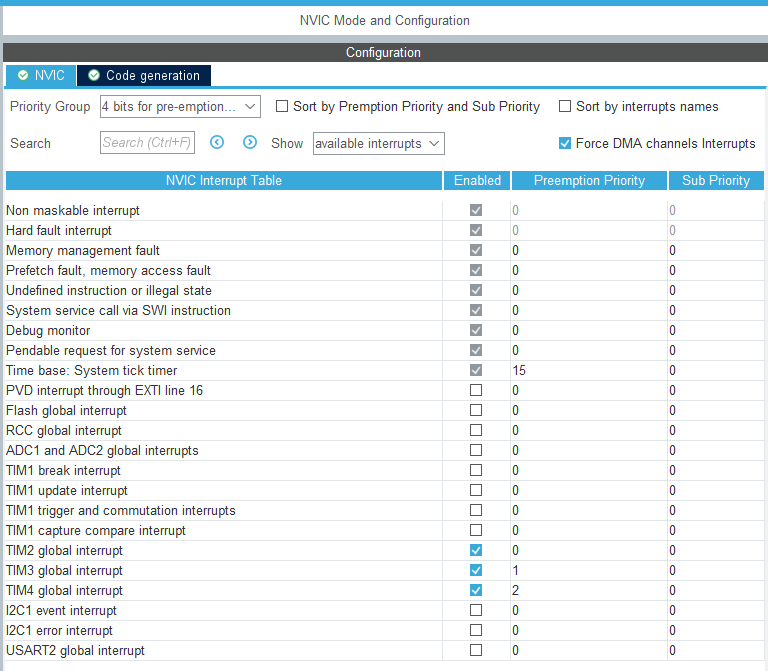
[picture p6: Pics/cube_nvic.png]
cube_nvic


+ 定时器：

公式：
$$
T=(ARR+1)*(PSC+1)/f_{ck}
$$

$$
f=\frac{1}{T}
$$

$f_{ck}$单位为Hz，对于STM32F103C8T6，$f_{ck}=72\times10^6$Hz；$T$单位为s。

| 定时器 | 分频值 | 重装值 | 周期 | 频率 | 功能简介 |
| --- | --- | --- | --- | --- | --- |
| TIM1 | 3-1 | 1500-1 | 62.5us | 16kHz | 生成PWM波&电流采样 |
| TIM2 | 300-1  | 240-1  | 1ms | 1000Hz | 编码器采样 |
| TIM3 | 160-1  | 72-1 | 160us  | 6.25kHz  | 电流环控制 |
| TIM4 | 160-1  | 144-1  | 320us  | 3.125kHz | 位置环&速度环控制  |

## 4.通讯协议

采用16Bit串行数据TTL&CAN通讯。TTL用于调参，CAN用于实时通信。详见：[通信协议说明](https://github.com/roboticszeng/GIA_ZENG/tree/main/Communication)

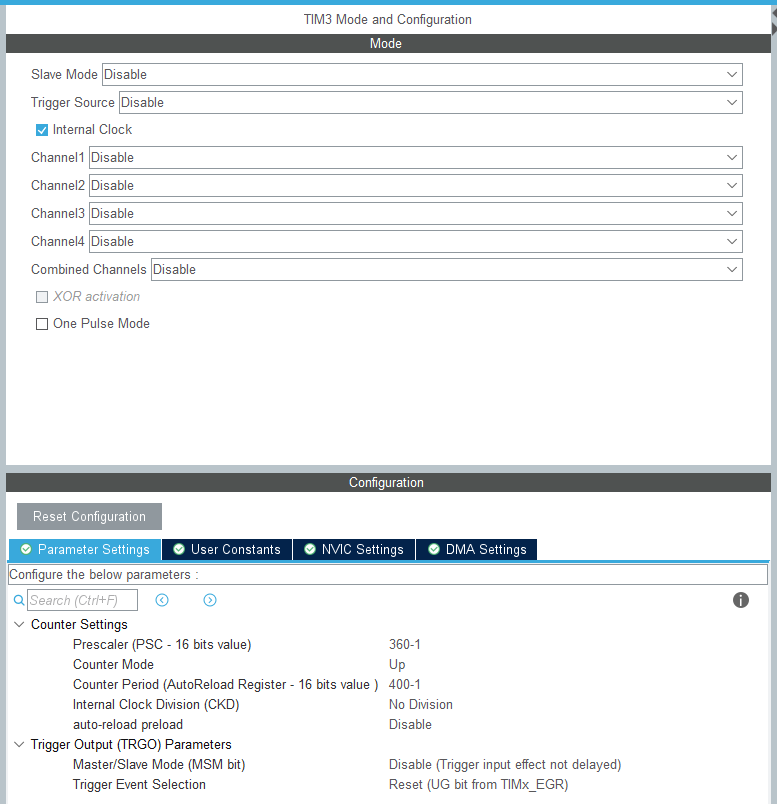
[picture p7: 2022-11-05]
Pics/cube_tim3.png

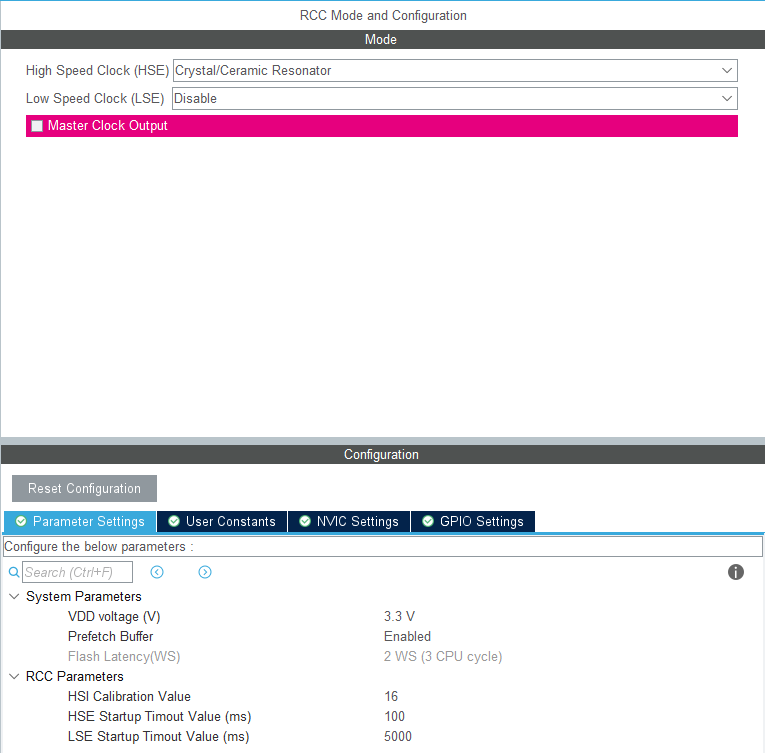
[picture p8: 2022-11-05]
Pics/cube_rcc.png

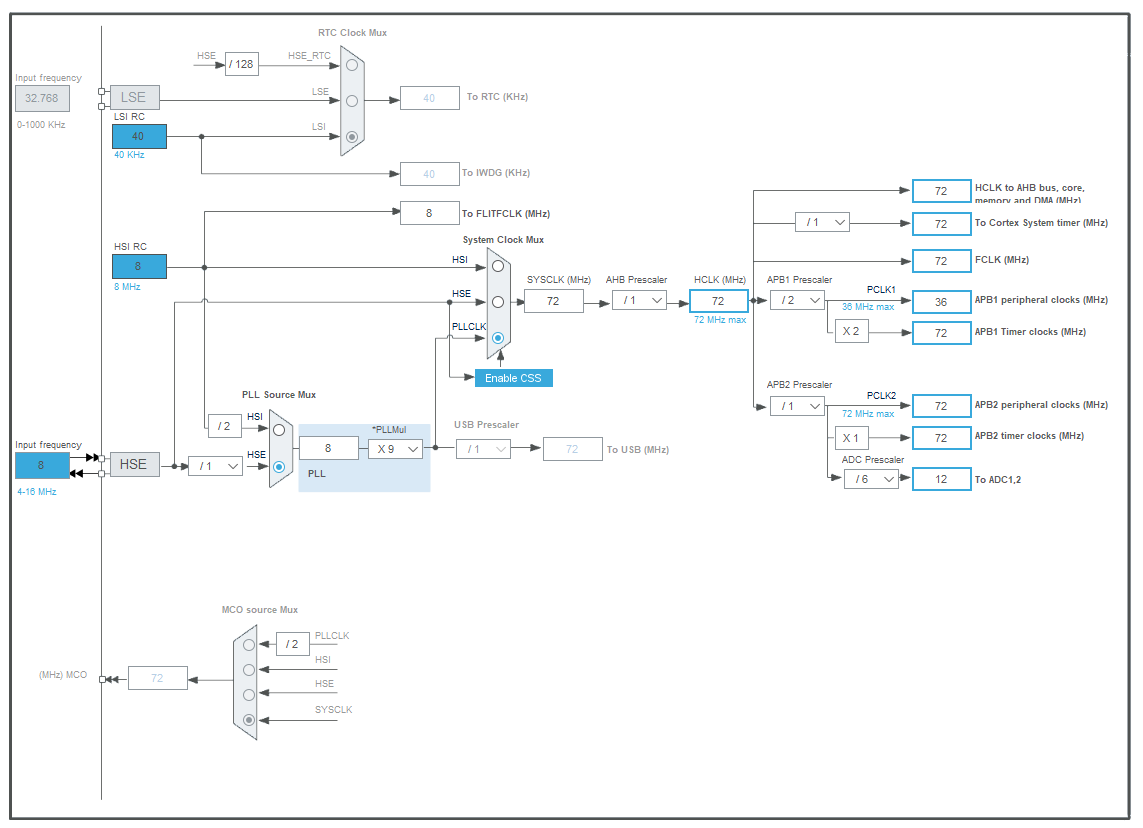
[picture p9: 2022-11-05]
Pics/cube_clock.png

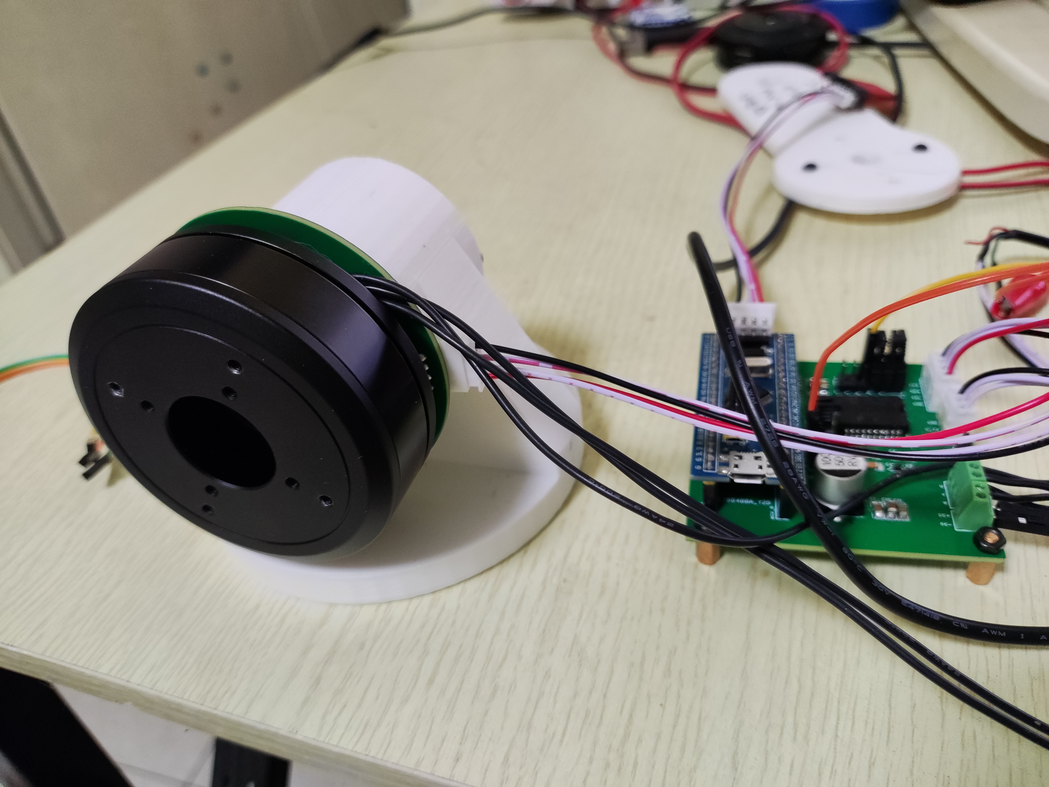
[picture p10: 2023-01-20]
Pics/motor_driver_pic.jpg

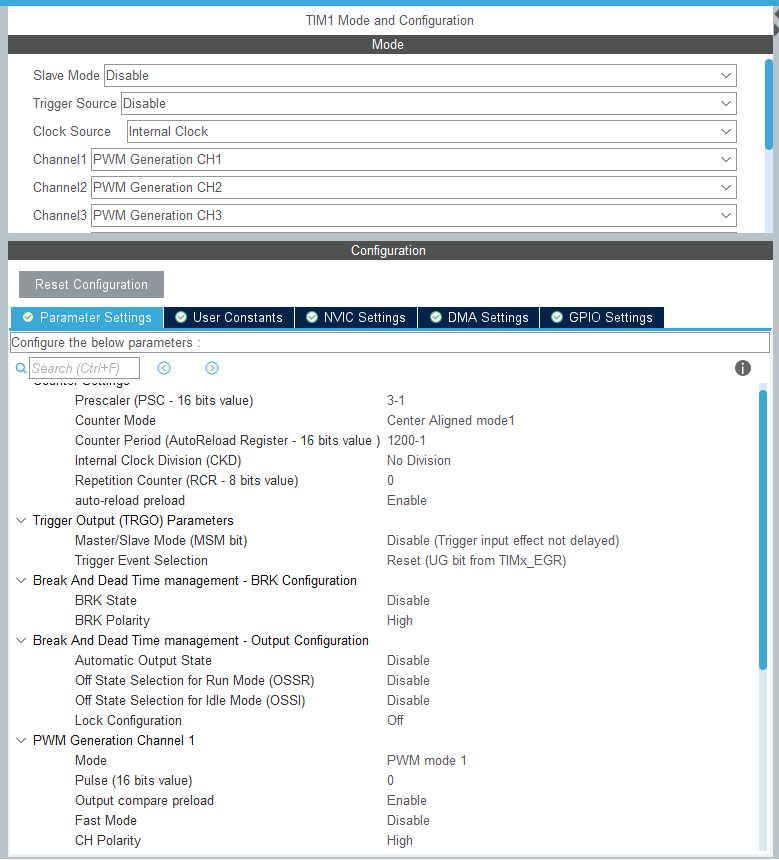
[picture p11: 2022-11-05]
Pics/cube_tim1.png

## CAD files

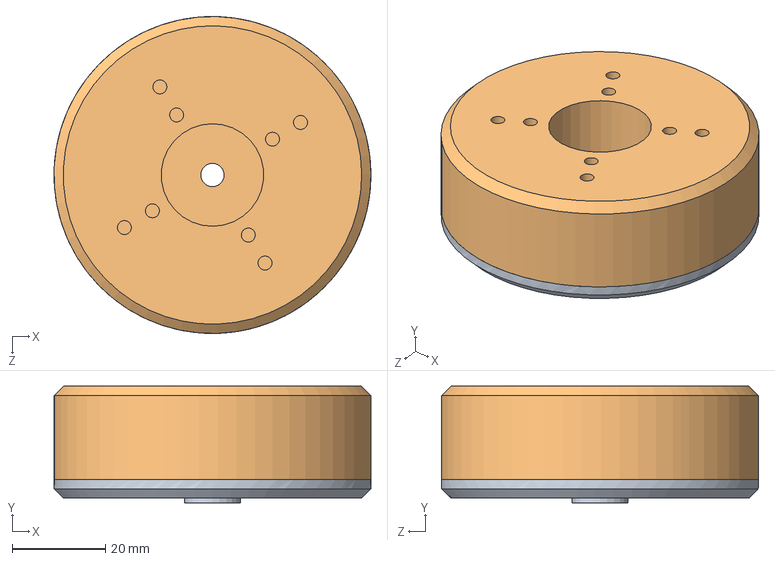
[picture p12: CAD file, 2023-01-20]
Structure/电机.SLDASM
68.0 x 25.0 x 68.0 mm
电机定子座
电机外转子

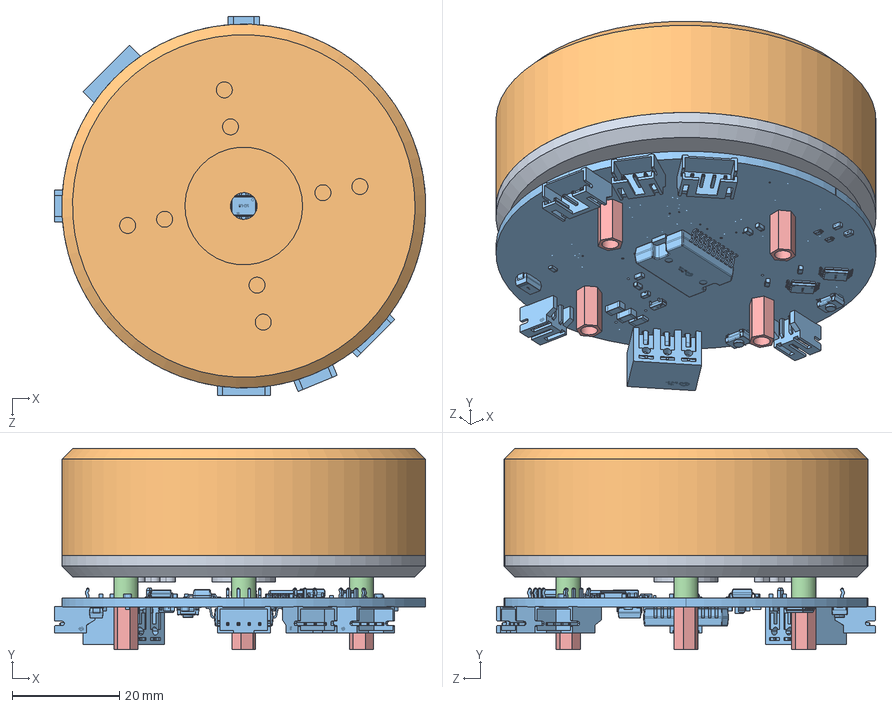
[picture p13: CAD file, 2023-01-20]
Structure/GIA_总装配.SLDASM
69.4 x 37.6 x 70.8 mm
电机定子座
电机外转子
驱动器
隔离脚 x 4
铜柱脚 x 4

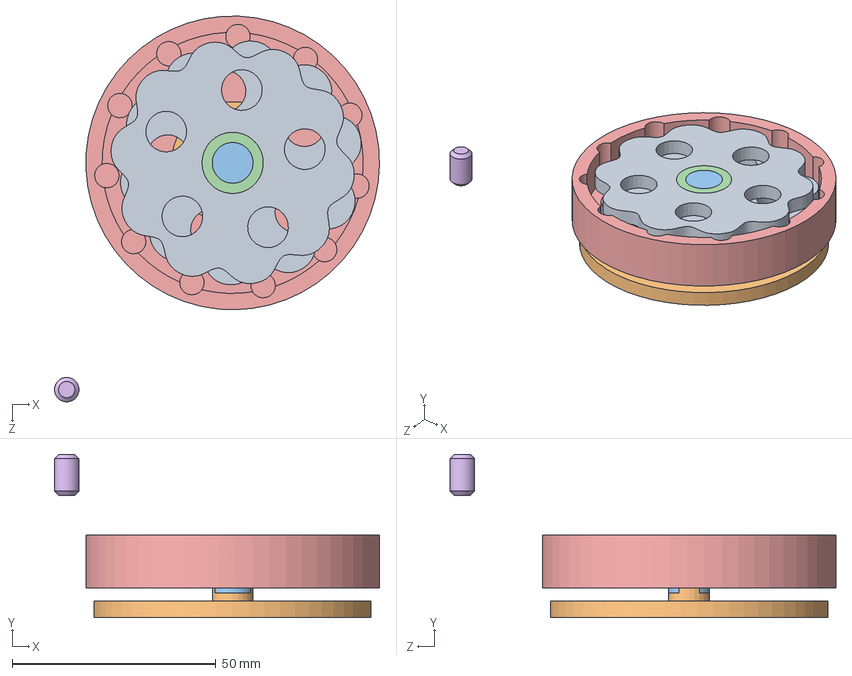
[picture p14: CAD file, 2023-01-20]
Structure/减速器.SLDASM
79.7 x 40.0 x 94.6 mm
摆线盘 x 2
电机转接盘
偏心轴
轴承 x 2
减速器上座
销

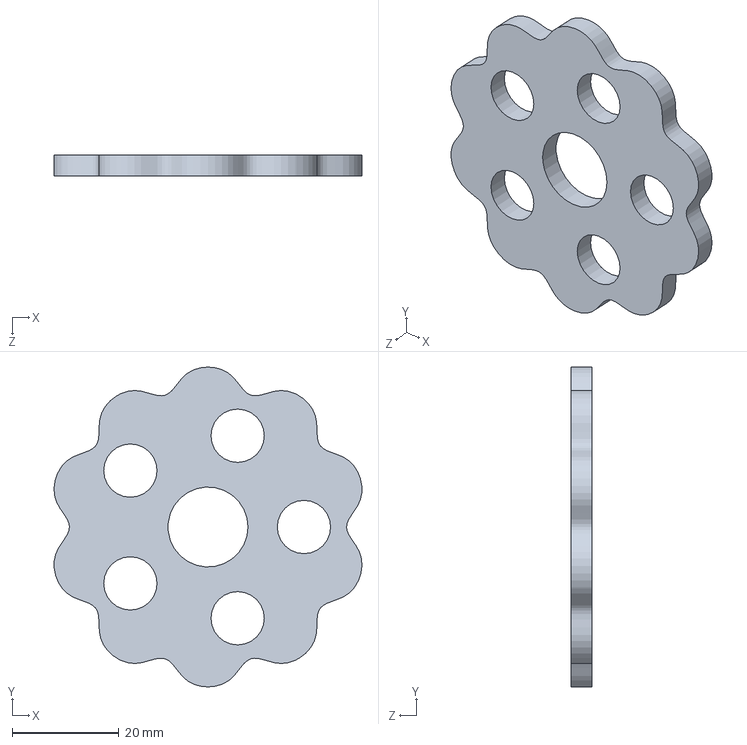
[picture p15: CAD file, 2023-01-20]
Structure/摆线盘.SLDPRT
57.8 x 60.0 x 4.00 mm

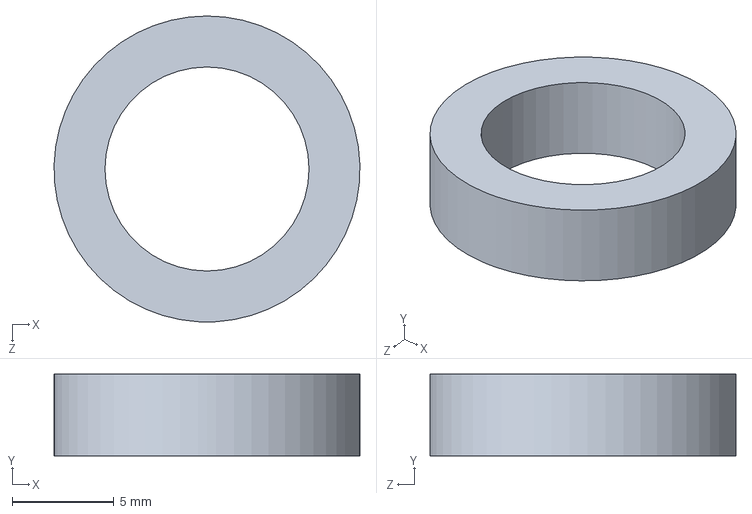
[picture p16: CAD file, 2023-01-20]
Structure/轴承.SLDPRT
15.0 x 4.00 x 15.0 mm

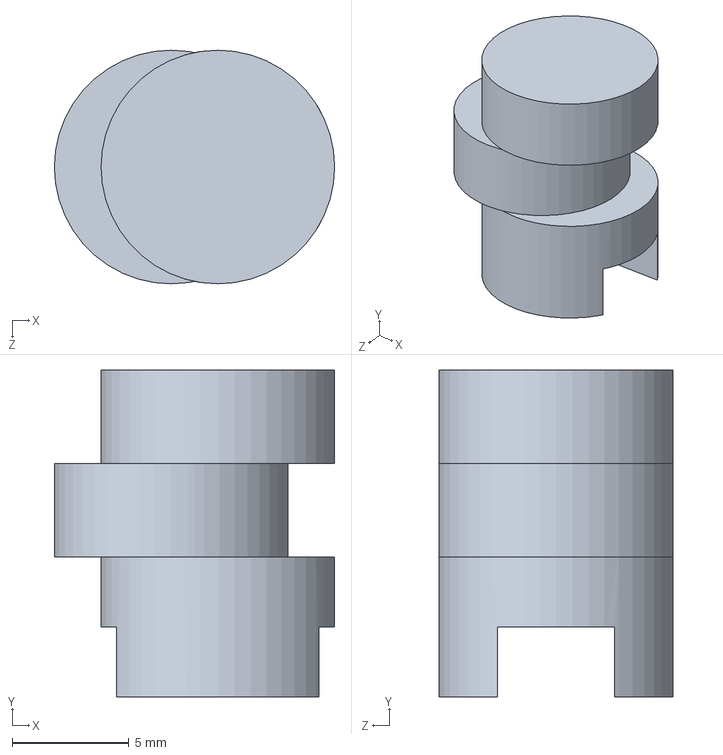
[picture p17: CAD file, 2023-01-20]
Structure/偏心轴.SLDPRT
12.0 x 14.0 x 10.0 mm

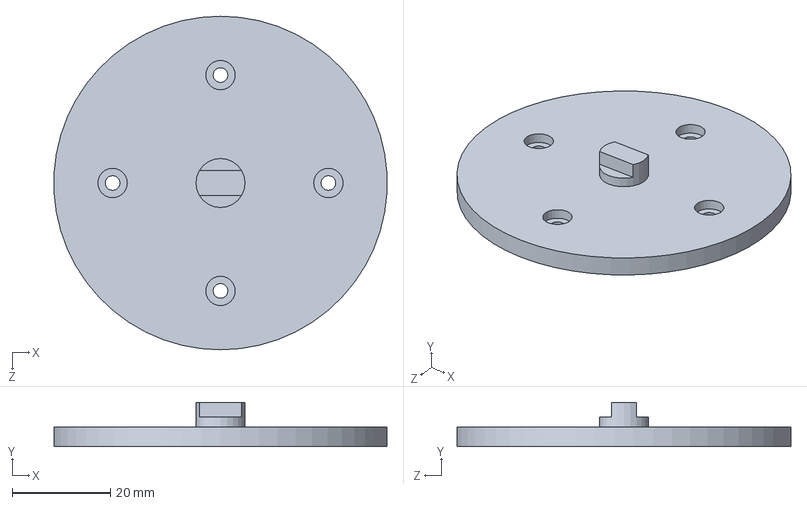
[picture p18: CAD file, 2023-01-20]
Structure/电机转接盘.SLDPRT
67.9 x 9.00 x 68.0 mm

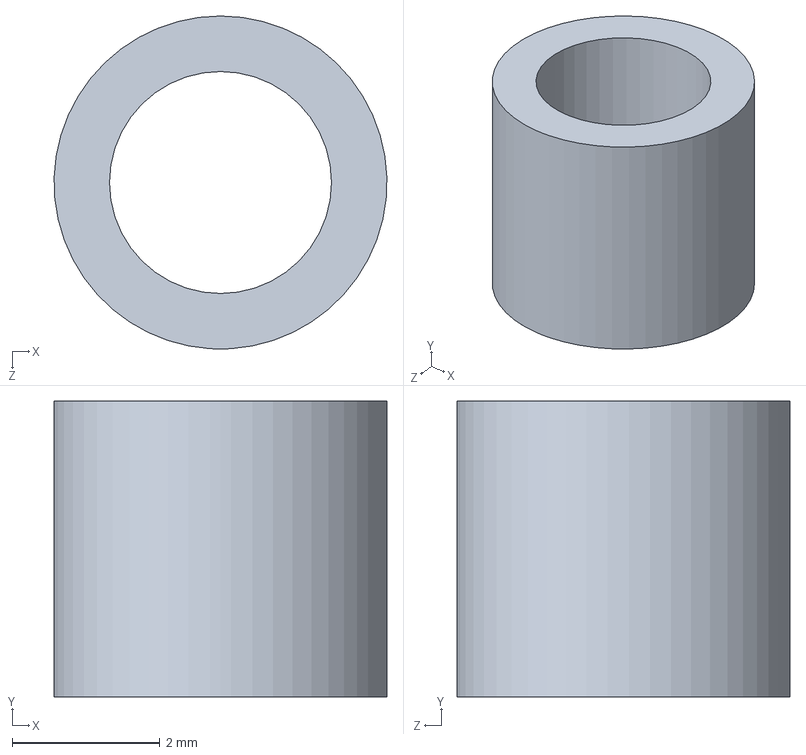
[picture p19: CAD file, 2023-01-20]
Structure/隔离脚.SLDPRT
4.50 x 4.00 x 4.50 mm

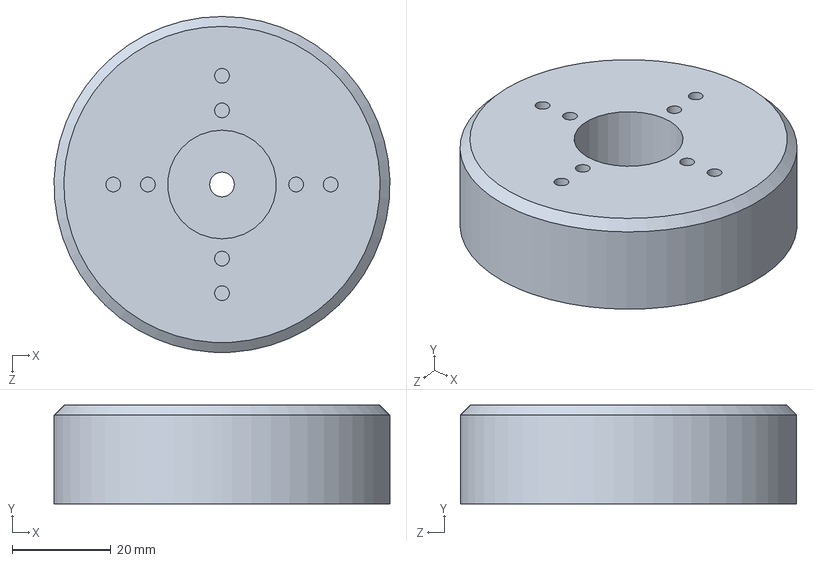
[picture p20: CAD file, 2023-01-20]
Structure/电机外转子.SLDPRT
68.0 x 20.0 x 68.0 mm

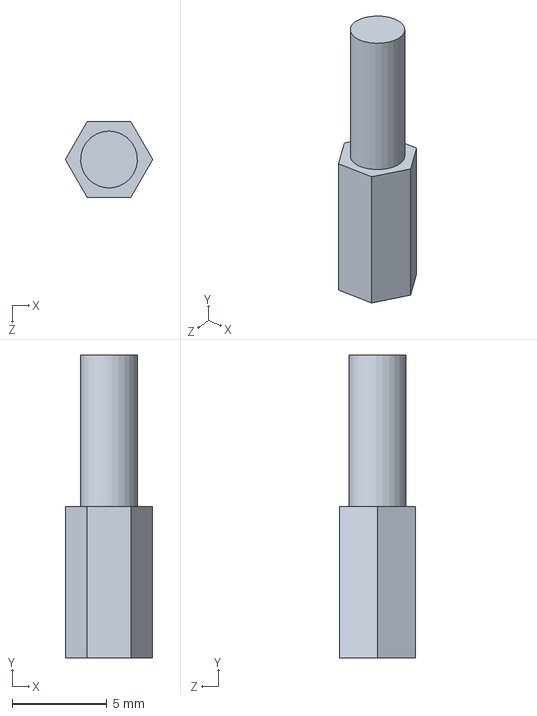
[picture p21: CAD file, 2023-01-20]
Structure/铜柱脚.SLDPRT
4.62 x 16.0 x 4.00 mm

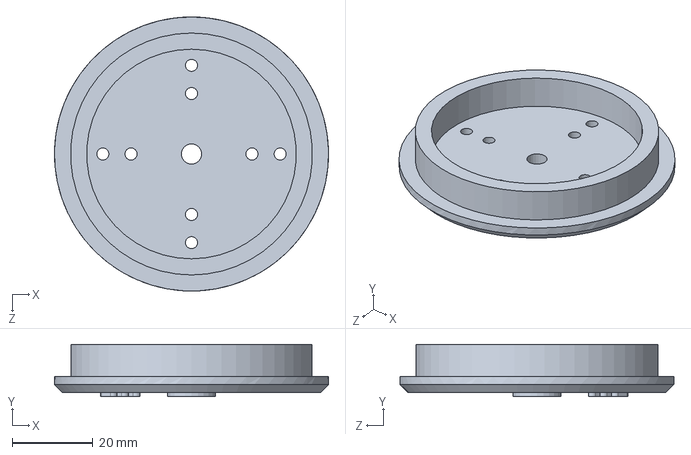
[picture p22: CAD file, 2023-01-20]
Structure/电机定子座.SLDPRT
68.0 x 13.0 x 68.0 mm

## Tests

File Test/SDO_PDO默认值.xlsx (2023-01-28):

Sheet: PDO
ADDR_MODE_OF_OPERATION | 0X3001
ADDR_TARGET_POSITION | 0X3002
ADDR_TARGET_VELOCITY | 0X3003
ADDR_VELOCITY_OFFSET | 0X3004
ADDR_TARGET_CURRENT_Q | 0X3005
ADDR_TORQUE_OFFSET | 0X3006
ADDR_MODE_OF_OPERATION_DISPLAY | 0X3081
ADDR_ACTUAL_POSITION | 0X3082
ADDR_FOLLOWING_ERROR | 0X3084
ADDR_ACTUAL_VELOCITY | 0X3085
ADDR_ACTUAL_CURRENT_Q | 0X308E
ADDR_ACTUAL_CURRENT_D | 0X308D
ADDR_PDO_SEND | 0x3080

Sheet: SDO
ADDR | ID | DEFAULT_VALUE
ADDR_ID | 0x3000 | 0
ADDR_ENC_ZERO_POSITION_H | 0x3500 | 0
ADDR_ENC_ZERO_POSITION_L | 0x3502 | 2048
ADDR_PID_POS_KP_INT | 0x3600 | 20
ADDR_PID_POS_KP_DEC | 0x3602 | 52429
ADDR_PID_POS_KI_INT | 0x3604 | 0
ADDR_PID_POS_KI_DEC | 0x3606 | 0
ADDR_PID_POS_MAX | 0x3608 | 3840
ADDR_PID_POS_INTMAX | 0x360a | 3840
ADDR_PID_VEL_KP_INT | 0x3610 | 0
ADDR_PID_VEL_KP_DEC | 0x3612 | 13107
ADDR_PID_VEL_KI_INT | 0x3614 | 1
ADDR_PID_VEL_KI_DEC | 0x3616 | 32768
ADDR_PID_VEL_MAX | 0x3618 | 512
ADDR_PID_VEL_INTMAX | 0x361a | 384
ADDR_PID_CUR_Q_KP_INT | 0x3620 | 0
ADDR_PID_CUR_Q_KP_DEC | 0x3622 | 52429
ADDR_PID_CUR_Q_KI_INT | 0x3624 | 40
ADDR_PID_CUR_Q_KI_DEC | 0x3626 | 0
ADDR_PID_CUR_Q_MAX | 0x3628 | 230
ADDR_PID_CUR_Q_INTMAX | 0x362a | 128
ADDR_PID_CUR_D_KP_INT | 0x3630 | 0
ADDR_PID_CUR_D_KP_DEC | 0x3632 | 13107
ADDR_PID_CUR_D_KI_INT | 0x3634 | 0
ADDR_PID_CUR_D_KI_DEC | 0x3636 | 0
ADDR_PID_CUR_D_MAX | 0x3638 | 51
ADDR_PID_CUR_D_INTMAX | 0x363a | 26
ADDR_FILT_VEL_CUTOFF_FREQ | 0x3702 | 20
ADDR_FILT_CUR_Q_CUTOFF_FREQ | 0x3704 | 20
ADDR_FILT_CUR_D_CUTOFF_FREQ | 0x3706 | 20
ADDR_POSITION_LOWER_LIMIT | 0x3800 | 0
ADDR_POSITION_UPPER_LIMIT | 0x3802 | 4096
ADDR_VELOCITY_LOWER_LIMIT | 0x3804 | 24000
ADDR_VELOCITY_UPPER_LIMIT | 0x3806 | 41000
ADDR_CURRENT_Q_LOWER_LIMIT | 0x3808 | 800
ADDR_CURRENT_Q_UPPER_LIMIT | 0x380a | 3300
ADDR_CURRENT_D_LOWER_LIMIT | 0x380c | 0
ADDR_CURRENT_D_UPPER_LIMIT | 0x380e | 4096
ADDR_ELEC_ZERO_POSITION | 0x3900
ADDR_ADC0_OFFSET | 0x3a00
ADDR_ADC1_OFFSET | 0x3a02

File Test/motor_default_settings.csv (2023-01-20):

序号 | 系统时间 | 时间标识 | CAN通道 | 传输方向 | ID号 | 帧类型 | 帧格式 | 长度 | 数据
0 | 12:08:1 | 无 | ch1 | 发送 | 0x3000 | 数据帧 | 扩展帧 | 0x08 | x| 55 00 00 00 00 00 0d 0a
1 | 12:08:2 | 无 | ch1 | 发送 | 0x3500 | 数据帧 | 扩展帧 | 0x08 | x| 55 00 00 00 00 00 0d 0a
2 | 12:08:3 | 无 | ch1 | 发送 | 0x3502 | 数据帧 | 扩展帧 | 0x08 | x| 55 00 08 00 00 00 0d 0a
3 | 12:08:4 | 无 | ch1 | 发送 | 0x3600 | 数据帧 | 扩展帧 | 0x08 | x| 55 00 00 14 00 00 0d 0a
4 | 12:08:5 | 无 | ch1 | 发送 | 0x3602 | 数据帧 | 扩展帧 | 0x08 | x| 55 00 00 00 00 00 0d 0a
5 | 12:08:6 | 无 | ch1 | 发送 | 0x3604 | 数据帧 | 扩展帧 | 0x08 | x| 55 00 00 00 00 00 0d 0a
6 | 12:08:7 | 无 | ch1 | 发送 | 0x3606 | 数据帧 | 扩展帧 | 0x08 | x| 55 00 00 00 00 00 0d 0a
7 | 12:08:8 | 无 | ch1 | 发送 | 0x3608 | 数据帧 | 扩展帧 | 0x08 | x| 55 00 0F 00 00 00 0d 0a
8 | 12:08:9 | 无 | ch1 | 发送 | 0x360a | 数据帧 | 扩展帧 | 0x08 | x| 55 00 0F 00 00 00 0d 0a
9 | 12:08:10 | 无 | ch1 | 发送 | 0x3610 | 数据帧 | 扩展帧 | 0x08 | x| 55 00 00 00 00 00 0d 0a
10 | 12:08:11 | 无 | ch1 | 发送 | 0x3612 | 数据帧 | 扩展帧 | 0x08 | x| 55 00 1A 9A 00 00 0d 0a
11 | 12:08:12 | 无 | ch1 | 发送 | 0x3614 | 数据帧 | 扩展帧 | 0x08 | x| 55 00 00 02 00 00 0d 0a
12 | 12:08:13 | 无 | ch1 | 发送 | 0x3616 | 数据帧 | 扩展帧 | 0x08 | x| 55 00 00 00 00 00 0d 0a
13 | 12:08:14 | 无 | ch1 | 发送 | 0x3618 | 数据帧 | 扩展帧 | 0x08 | x| 55 00 02 00 00 00 0d 0a
14 | 12:08:15 | 无 | ch1 | 发送 | 0x361a | 数据帧 | 扩展帧 | 0x08 | x| 55 00 02 80 00 00 0d 0a
15 | 12:08:16 | 无 | ch1 | 发送 | 0x3620 | 数据帧 | 扩展帧 | 0x08 | x| 55 00 00 00 00 00 0d 0a
16 | 12:08:17 | 无 | ch1 | 发送 | 0x3622 | 数据帧 | 扩展帧 | 0x08 | x| 55 00 CD CD 00 00 0d 0a
17 | 12:08:18 | 无 | ch1 | 发送 | 0x3624 | 数据帧 | 扩展帧 | 0x08 | x| 55 00 00 28 00 00 0d 0a
18 | 12:08:19 | 无 | ch1 | 发送 | 0x3626 | 数据帧 | 扩展帧 | 0x08 | x| 55 00 00 00 00 00 0d 0a
19 | 12:08:20 | 无 | ch1 | 发送 | 0x3628 | 数据帧 | 扩展帧 | 0x08 | x| 55 00 01 E6 00 00 0d 0a
20 | 12:08:21 | 无 | ch1 | 发送 | 0x362a | 数据帧 | 扩展帧 | 0x08 | x| 55 00 01 80 00 00 0d 0a
21 | 12:08:22 | 无 | ch1 | 发送 | 0x3630 | 数据帧 | 扩展帧 | 0x08 | x| 55 00 00 00 00 00 0d 0a
22 | 12:08:23 | 无 | ch1 | 发送 | 0x3632 | 数据帧 | 扩展帧 | 0x08 | x| 55 00 33 33 00 00 0d 0a
23 | 12:08:24 | 无 | ch1 | 发送 | 0x3634 | 数据帧 | 扩展帧 | 0x08 | x| 55 00 00 00 00 00 0d 0a
24 | 12:08:25 | 无 | ch1 | 发送 | 0x3636 | 数据帧 | 扩展帧 | 0x08 | x| 55 00 00 00 00 00 0d 0a
25 | 12:08:26 | 无 | ch1 | 发送 | 0x3638 | 数据帧 | 扩展帧 | 0x08 | x| 55 00 00 33 00 00 0d 0a
26 | 12:08:27 | 无 | ch1 | 发送 | 0x363a | 数据帧 | 扩展帧 | 0x08 | x| 55 00 00 1A 00 00 0d 0a
27 | 12:08:28 | 无 | ch1 | 发送 | 0x3702 | 数据帧 | 扩展帧 | 0x08 | x| 55 00 00 14 00 00 0d 0a
28 | 12:08:29 | 无 | ch1 | 发送 | 0x3704 | 数据帧 | 扩展帧 | 0x08 | x| 55 00 00 14 00 00 0d 0a
29 | 12:08:30 | 无 | ch1 | 发送 | 0x3706 | 数据帧 | 扩展帧 | 0x08 | x| 55 00 00 14 00 00 0d 0a
30 | 12:08:31 | 无 | ch1 | 发送 | 0x3800 | 数据帧 | 扩展帧 | 0x08 | x| 55 00 00 00 00 00 0d 0a
31 | 12:08:32 | 无 | ch1 | 发送 | 0x3802 | 数据帧 | 扩展帧 | 0x08 | x| 55 00 10 00 00 00 0d 0a
32 | 12:08:33 | 无 | ch1 | 发送 | 0x3804 | 数据帧 | 扩展帧 | 0x08 | x| 55 00 5E C0 00 00 0d 0a
33 | 12:08:34 | 无 | ch1 | 发送 | 0x3806 | 数据帧 | 扩展帧 | 0x08 | x| 55 00 A0 28 00 00 0d 0a
34 | 12:08:35 | 无 | ch1 | 发送 | 0x3808 | 数据帧 | 扩展帧 | 0x08 | x| 55 00 03 20 00 00 0d 0a
35 | 12:08:36 | 无 | ch1 | 发送 | 0x380a | 数据帧 | 扩展帧 | 0x08 | x| 55 00 0D E4 00 00 0d 0a
36 | 12:08:37 | 无 | ch1 | 发送 | 0x380c | 数据帧 | 扩展帧 | 0x08 | x| 55 00 00 00 00 00 0d 0a
37 | 12:08:38 | 无 | ch1 | 发送 | 0x380e | 数据帧 | 扩展帧 | 0x08 | x| 55 00 10 00 00 00 0d 0a

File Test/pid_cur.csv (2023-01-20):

序号 | 系统时间 | 时间标识 | CAN通道 | 传输方向 | ID号 | 帧类型 | 帧格式 | 长度 | 数据
0 | 12:08:1 | 无 | ch1 | 发送 | 0x3620 | 数据帧 | 扩展帧 | 0x08 | x| 55 00 00 00 00 00 0d 0a
1 | 12:08:2 | 无 | ch1 | 发送 | 0x3622 | 数据帧 | 扩展帧 | 0x08 | x| 55 00 CD CD 00 00 0d 0a
2 | 12:08:3 | 无 | ch1 | 发送 | 0x3624 | 数据帧 | 扩展帧 | 0x08 | x| 55 00 00 28 00 00 0d 0a
3 | 12:08:4 | 无 | ch1 | 发送 | 0x3626 | 数据帧 | 扩展帧 | 0x08 | x| 55 00 00 00 00 00 0d 0a
4 | 12:08:5 | 无 | ch1 | 发送 | 0x3628 | 数据帧 | 扩展帧 | 0x08 | x| 55 00 01 E6 00 00 0d 0a
5 | 12:08:6 | 无 | ch1 | 发送 | 0x362a | 数据帧 | 扩展帧 | 0x08 | x| 55 00 01 80 00 00 0d 0a
6 | 12:08:7 | 无 | ch1 | 发送 | 0x3630 | 数据帧 | 扩展帧 | 0x08 | x| 55 00 00 00 00 00 0d 0a
7 | 12:08:8 | 无 | ch1 | 发送 | 0x3632 | 数据帧 | 扩展帧 | 0x08 | x| 55 00 33 33 00 00 0d 0a

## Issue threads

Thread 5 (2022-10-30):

软件：编码器读取速率太低，整体控制频率被极大拉高

roboticszeng, 2022-10-30:
AS5600用I2C读取居然要500us，离谱

roboticszeng, 2022-11-14:
暂采用Fast Mode解决，参考了开源的代码优化读取程序。提高速率到250us以内，进一步的优化留给下一版本。
分支：dev_communication，版本：89c70f8858a733efc7a2e6258e2ae5e010a96ddd

roboticszeng, 2023-01-12:
这和香农定理不是一回事，读取速率仍设置为1000Hz不变。

Closed 2023-01-12.

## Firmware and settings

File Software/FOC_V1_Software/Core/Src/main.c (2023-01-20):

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
/* Includes ------------------------------------------------------------------*/
#include "main.h"
#include "adc.h"
#include "can.h"
#include "dma.h"
#include "i2c.h"
#include "tim.h"
#include "usart.h"
#include "gpio.h"

/* USER CODE BEGIN Includes */

#include "stdio.h"

int fgetc(FILE *f)
{
  uint8_t ch = 0;
  HAL_UART_Receive(&huart2, &ch, 1, 0xffff);
  return ch;
}

int fputc(int ch, FILE *f)
{
  HAL_UART_Transmit(&huart2, (uint8_t *)&ch, 1, 0xffff);
  return ch;
}

#include "controll.h"
#include "AS5600.h"
#include "can.h"
#include "flash.h"

/* USER CODE END Includes */


void SystemClock_Config(void);
/* USER CODE BEGIN 0 */

uint16_t ADDR_ARRAY[] = {ADDR_ID,
                         ADDR_ENC_ZERO_POSITION_H, ADDR_ENC_ZERO_POSITION_L, 
                         ADDR_PID_POS_KP_INT, ADDR_PID_POS_KP_DEC, ADDR_PID_POS_KI_INT, ADDR_PID_POS_KI_DEC, ADDR_PID_POS_MAX, ADDR_PID_POS_INTMAX,
                         ADDR_PID_VEL_KP_INT, ADDR_PID_VEL_KP_DEC, ADDR_PID_VEL_KI_INT, ADDR_PID_VEL_KI_DEC, ADDR_PID_VEL_MAX, ADDR_PID_VEL_INTMAX,
                         ADDR_PID_CUR_Q_KP_INT, ADDR_PID_CUR_Q_KP_DEC, ADDR_PID_CUR_Q_KI_INT, ADDR_PID_CUR_Q_KI_DEC, ADDR_PID_CUR_Q_MAX, ADDR_PID_CUR_Q_INTMAX,
                         ADDR_PID_CUR_D_KP_INT, ADDR_PID_CUR_D_KP_DEC, ADDR_PID_CUR_D_KI_INT, ADDR_PID_CUR_D_KI_DEC, ADDR_PID_CUR_D_MAX, ADDR_PID_CUR_D_INTMAX,
                         ADDR_FILT_VEL_CUTOFF_FREQ, ADDR_FILT_CUR_Q_CUTOFF_FREQ, ADDR_FILT_CUR_D_CUTOFF_FREQ,
                         ADDR_POSITION_LOWER_LIMIT, ADDR_POSITION_UPPER_LIMIT, ADDR_VELOCITY_LOWER_LIMIT, ADDR_VELOCITY_UPPER_LIMIT,
                         ADDR_CURRENT_Q_LOWER_LIMIT, ADDR_CURRENT_Q_UPPER_LIMIT, ADDR_CURRENT_D_LOWER_LIMIT, ADDR_CURRENT_D_UPPER_LIMIT,
                         ADDR_ELEC_ZERO_POSITION,
                         ADDR_ADC0_OFFSET, ADDR_ADC1_OFFSET};

// can test
CAN_TxHeaderTypeDef Can_Tx;
CAN_RxHeaderTypeDef Can_Rx;
uint8_t Rxdata[8];
uint8_t Txdata[8] = {0};
extern uint8_t can_rx_finish_flag;

extern _iq const_point;
extern uint16_t adc_dma_buf[NUMBER_ADC_CHANNEL * NUMBER_ADC_CHANNEL_AVERAGE_PER_CHANNEL];

encoder_typedef *oEncoder;
config_typedef *oConfig;
state_typedef *oState;

pid_typedef *oPidPosition;
pid_typedef *oPidVelocity;
pid_typedef *oPidCurrentD;
pid_typedef *oPidCurrentQ;

filter_typedef *oFilterVelocity;
filter_typedef *oFilterCurrentD;
filter_typedef *oFilterCurrentQ;

sdo_typedef *oSdo;
pdo_typedef *oPdo;

/* USER CODE END 0 */

/**
 * @brief  The application entry point.
 * @retval int
 */
int main(void)
{
  /* MCU Configuration--------------------------------------------------------*/

  /* Reset of all peripherals, Initializes the Flash interface and the Systick. */
  HAL_Init();

  /* Configure the system clock */
  SystemClock_Config();

  /* Initialize all configured peripherals */
  MX_GPIO_Init();
  MX_DMA_Init();
  MX_TIM1_Init();
  MX_USART2_UART_Init();
  MX_ADC1_Init();
  MX_I2C1_Init();
  MX_TIM2_Init();
  MX_TIM3_Init();
  MX_TIM4_Init();
  MX_CAN_Init();
  /* USER CODE BEGIN 2 */
  HAL_GPIO_WritePin(DRV_EN_GPIO_Port, DRV_EN_Pin, GPIO_PIN_SET);
  HAL_GPIO_WritePin(GPIOC, GPIO_PIN_13, GPIO_PIN_RESET);
  HAL_GPIO_WritePin(SENS_DIR_GPIO_Port, SENS_DIR_Pin, GPIO_PIN_RESET);
  HAL_ADC_Start_DMA(&hadc1, (uint32_t *)adc_dma_buf, NUMBER_ADC_CHANNEL * NUMBER_ADC_CHANNEL_AVERAGE_PER_CHANNEL);
  
  HAL_TIM_PWM_Start(&htim1, TIM_CHANNEL_1);
  HAL_TIM_PWM_Start(&htim1, TIM_CHANNEL_2);
  HAL_TIM_PWM_Start(&htim1, TIM_CHANNEL_3);
  
  // 上电时的先后逻辑需要重新check


  // 分配所有空间
  oEncoder = as5600_new();
  oEncoder->i2c_handle = &hi2c1;
  oEncoder->dir_port = SENS_DIR_GPIO_Port;
  oEncoder->dir_pin = SENS_DIR_Pin;
  oState = state_new();
  oPdo = pdo_new();
  oSdo = sdo_new();
  oConfig = config_new();

  oPidPosition = pid_new();
  oPidVelocity = pid_new();
  oPidCurrentQ = pid_new();
  oPidCurrentD = pid_new();

  oFilterVelocity = filter_new();
  oFilterCurrentD = filter_new();
  oFilterCurrentQ = filter_new();


  // 初始化as5600
  as5600_init(oEncoder);
  
  // 初始化pdo，状态量由pdo生成；主要是对目标值进行初始化：位置pi，速度0，电流0，模式0
  pdo_init(oPdo);
  // 初始化状态量，感觉这里可有可无，待测试
  state_init(oState);



  // 初始化sdo
  read_config(oSdo);

  // 初始化config, pid, filter
  para_init(oSdo, oConfig);

  CAN_User_Init(&hcan);
  
  HAL_TIM_Base_Start_IT(&htim1);
  HAL_TIM_Base_Start_IT(&htim2);
  HAL_TIM_Base_Start_IT(&htim3);
  HAL_TIM_Base_Start_IT(&htim4);

  HAL_Delay(1000);

  /* USER CODE END 2 */

  /* Infinite loop */
  /* USER CODE BEGIN WHILE */
  while (1)
  {

    printf("%.4f, %.4f, %.4f, %.4f, %.4f, %.4f, %.4f, ", \
        _IQtoF(oState->iqPos), _IQtoF(oState->iqTargP), _IQtoF(oState->iqVel), _IQtoF(oState->iqTargV), \
        _IQtoF(oState->iqCurQ), _IQtoF(oState->iqTargQ), _IQtoF(oState->iqVoltQ));
      
//      printf("%.4f, %.4f, %.4f, %.4f, ", _IQ15toF(oPidPosition->Kp), _IQ15toF(oPidPosition->Ki), _IQ15toF(oPidPosition->integrator), \
//        _IQ15toF(oPidPosition->out));
      
      printf("%.4f, %.4f, %.4f, %.4f, ", _IQ15toF(oPidVelocity->Kp), _IQ15toF(oPidVelocity->Ki), _IQ15toF(oPidVelocity->integrator), \
        _IQ15toF(oPidVelocity->out));

//      printf("%.4f, %.4f, %.4f, %.4f, ", _IQ15toF(oPidCurrentQ->Kp), _IQ15toF(oPidCurrentQ->Ki), _IQ15toF(oPidCurrentQ->integrator), \
//        _IQ15toF(oPidCurrentQ->out));
      
//      printf("%.4f, %.4f, %.4f, %.4f, ", _IQ15toF(oPidCurrentD->Kp), _IQ15toF(oPidCurrentD->Ki), _IQ15toF(oPidCurrentD->integrator), \
//        _IQ15toF(oPidCurrentD->out));
      
//      printf("%d, %.4f, %d\r\n", oConfig->ELEC_ZERO_POSITION, _IQtoF(oState->iqPosElec), oPdo->PDO_ACTUAL_POSITION);
//      printf("%d, %d\r\n", oConfig->CONST_ADC0_OFFSET, oConfig->CONST_ADC1_OFFSET);

      printf("\r\n");
    HAL_Delay(100);

    /* USER CODE END WHILE */

    /* USER CODE BEGIN 3 */
  }
  /* USER CODE END 3 */
}

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


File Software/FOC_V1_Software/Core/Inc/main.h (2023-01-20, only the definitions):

#define LED_BLINK_READ_FLASH 10
#define LED_BLINK_SAVE_FLASH 4
#define LED_BLINK_CALIB 2
#define PWM_PERIOD (1500-1)
#define DATA_WRITE_HEAD 0x55
#define DATA_READ_HEAD 0x56
#define DATA_TAIL_PREV 0x0d
#define DATA_TAIL 0x0a
#define DATA_READ_FLAG 0xaaaa
#define DATA_ERROR 0xffff
#define MODE_CSP 0x08
#define MODE_CSV 0x09
#define MODE_CST 0x0a
#define MODE_NO  0x00
#define PID_INDEX_POS 0x08
#define PID_INDEX_VEL 0x09
#define PID_INDEX_CUR_Q 0x0a
#define PID_INDEX_CUR_D 0x0b
#define FILTER_INDEX_POS 0x08
#define FILTER_INDEX_VEL 0x09
#define FILTER_INDEX_CUR_Q 0x0a
#define FILTER_INDEX_CUR_D 0x0b
#define ADDR_MODE_OF_OPERATION 0X3001
#define ADDR_TARGET_POSITION 0X3002
#define ADDR_TARGET_VELOCITY 0X3003
#define ADDR_VELOCITY_OFFSET 0X3004
#define ADDR_TARGET_CURRENT_Q 0X3005
#define ADDR_TORQUE_OFFSET 0X3006
#define ADDR_MODE_OF_OPERATION_DISPLAY 0X3081
#define ADDR_ACTUAL_POSITION 0X3082
#define ADDR_FOLLOWING_ERROR 0X3084
#define ADDR_ACTUAL_VELOCITY 0X3085
#define ADDR_ACTUAL_CURRENT_Q 0X308E
#define ADDR_ACTUAL_CURRENT_D 0X308D
#define ADDR_PDO_SEND 0x3080
#define ADDR_ID 0x3000
#define ADDR_ENC_ZERO_POSITION_H 0X3500
#define ADDR_ENC_ZERO_POSITION_L 0X3502
#define ADDR_PID_POS_KP_INT 0x3600
#define ADDR_PID_POS_KP_DEC 0x3602
#define ADDR_PID_POS_KI_INT 0x3604
#define ADDR_PID_POS_KI_DEC 0x3606
#define ADDR_PID_POS_MAX 0x3608
#define ADDR_PID_POS_INTMAX 0x360a
#define ADDR_PID_VEL_KP_INT 0x3610
#define ADDR_PID_VEL_KP_DEC 0x3612
#define ADDR_PID_VEL_KI_INT 0x3614
#define ADDR_PID_VEL_KI_DEC 0x3616
#define ADDR_PID_VEL_MAX 0x3618
#define ADDR_PID_VEL_INTMAX 0x361a
#define ADDR_PID_CUR_Q_KP_INT 0x3620
#define ADDR_PID_CUR_Q_KP_DEC 0x3622
#define ADDR_PID_CUR_Q_KI_INT 0x3624
#define ADDR_PID_CUR_Q_KI_DEC 0x3626
#define ADDR_PID_CUR_Q_MAX 0x3628
#define ADDR_PID_CUR_Q_INTMAX 0x362a
#define ADDR_PID_CUR_D_KP_INT 0x3630
#define ADDR_PID_CUR_D_KP_DEC 0x3632
#define ADDR_PID_CUR_D_KI_INT 0x3634
#define ADDR_PID_CUR_D_KI_DEC 0x3636
#define ADDR_PID_CUR_D_MAX 0x3638
#define ADDR_PID_CUR_D_INTMAX 0x363a
#define ADDR_FILT_VEL_CUTOFF_FREQ 0x3702
#define ADDR_FILT_CUR_Q_CUTOFF_FREQ 0x3704
#define ADDR_FILT_CUR_D_CUTOFF_FREQ 0x3706
#define ADDR_POSITION_LOWER_LIMIT 0x3800
#define ADDR_POSITION_UPPER_LIMIT 0x3802
#define ADDR_VELOCITY_LOWER_LIMIT 0x3804
#define ADDR_VELOCITY_UPPER_LIMIT 0x3806
#define ADDR_CURRENT_Q_LOWER_LIMIT 0x3808
#define ADDR_CURRENT_Q_UPPER_LIMIT 0x380a
#define ADDR_CURRENT_D_LOWER_LIMIT 0x380c
#define ADDR_CURRENT_D_UPPER_LIMIT 0x380e
#define ADDR_ELEC_ZERO_POSITION 0x3900
#define ADDR_ADC0_OFFSET 0x3a00
#define ADDR_ADC1_OFFSET 0x3a02
#define ADDR_READ_FLAG 0x3f00
#define ADDR_READ_FLASH 0x3ffc
#define ADDR_SAVE_FLASH 0x3ffe
#define LED_Pin GPIO_PIN_13
#define LED_GPIO_Port GPIOC
#define SENS_DIR_Pin GPIO_PIN_4
#define SENS_DIR_GPIO_Port GPIOA
#define KEY_Pin GPIO_PIN_5
#define KEY_GPIO_Port GPIOA
#define KEY_EXTI_IRQn EXTI9_5_IRQn
#define DRV_EN_Pin GPIO_PIN_15
#define DRV_EN_GPIO_Port GPIOB
#define SENS_OUT_Pin GPIO_PIN_5
#define SENS_OUT_GPIO_Port GPIOB

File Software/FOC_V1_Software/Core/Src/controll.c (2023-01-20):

#include "controll.h"
#include "tim.h"
#include <math.h>
#include <AS5600.h>
#include "IQmathLib.h"
#include "adc.h"

extern encoder_typedef *oEncoder;

extern pid_typedef *oPidPosition;
extern pid_typedef *oPidVelocity;
extern pid_typedef *oPidCurrentD;
extern pid_typedef *oPidCurrentQ;

extern filter_typedef *oFilterVelocity;
extern filter_typedef *oFilterCurrentD;
extern filter_typedef *oFilterCurrentQ;

extern config_typedef *oConfig;


/***********************************************************************************************************************************************/
/*** PID ***/

pid_typedef *pid_new(void)
{

    return (pid_typedef *)calloc(1, sizeof(pid_typedef));
}

void pid_init(pid_typedef *handle, config_typedef *config, uint8_t pid_index)
{
    /* Clear controller variables */

    switch (pid_index)
    {
    case PID_INDEX_POS:
        handle->Kp = config->PID_POS_KP;
        handle->Ki = config->PID_POS_KI;
        handle->T = config->CONST_POSITION_CONTROL_TIME;
        handle->limMax = config->PID_POS_MAX;
        handle->limMaxInt = config->PID_POS_INTMAX;
        break;
    case PID_INDEX_VEL:
        handle->Kp = config->PID_VEL_KP;
        handle->Ki = config->PID_VEL_KI;
        // 速度环和位置环共用CONST_POSITION_CONTROL_TIME
        handle->T = config->CONST_POSITION_CONTROL_TIME;
        handle->limMax = config->PID_VEL_MAX;
        handle->limMaxInt = config->PID_VEL_INTMAX;
        break;
    case PID_INDEX_CUR_Q:
        handle->Kp = config->PID_CUR_Q_KP;
        handle->Ki = config->PID_CUR_Q_KI;
        handle->T = config->CONST_CURRENT_CONTROL_TIME;
        handle->limMax = config->PID_CUR_Q_MAX;
        handle->limMaxInt = config->PID_CUR_Q_INTMAX;
        break;
    case PID_INDEX_CUR_D:
        handle->Kp = config->PID_CUR_D_KP;
        handle->Ki = config->PID_CUR_D_KI;
        // 电流环共用CONST_CURRENT_CONTROL_TIME
        handle->T = config->CONST_CURRENT_CONTROL_TIME;
        handle->limMax = config->PID_CUR_D_MAX;
        handle->limMaxInt = config->PID_CUR_D_INTMAX;
        break;
    }

    handle->limMin = -handle->limMax;
    handle->limMinInt = -handle->limMaxInt;
    // 暂时不用Kd
    handle->Kd = _IQ15(0.0);
    handle->tau = _IQ15(0.0);
    handle->integrator = _IQ15(0.0);
    handle->prevError = _IQ15(0.0);
    handle->differentiator = _IQ15(0.0);
    handle->prevMeasurement = _IQ15(0.0);
    handle->out = _IQ15(0.0);
}

_iq pid_update(pid_typedef *pid, _iq setpoint, _iq measurement)
{

    static _iq15 error;
    error = _IQtoIQ15(setpoint) - _IQtoIQ15(measurement);

    pid->proportional = _IQ15mpy(pid->Kp, error);

    pid->integrator = pid->integrator + _IQ15mpyIQX(_IQmpy(_IQmpy(_IQ(0.5), _IQ15toIQ(pid->Ki)), pid->T), 20, (error + pid->prevError), 15);

    if (pid->integrator > pid->limMaxInt)
    {
        pid->integrator = pid->limMaxInt;
    }
    else if (pid->integrator < pid->limMinInt)
    {
        pid->integrator = pid->limMinInt;
    }
    //    pid->differentiator = -(2.0f * pid->Kd * (measurement - pid->prevMeasurement)	/* Note: derivative on measurement, therefore minus sign in front of equation! */
    //                        + (2.0f * pid->tau - pid->T) * pid->differentiator)
    //                        / (2.0f * pid->tau + pid->T);
    // 暂时不用KD
    pid->differentiator = _IQ15(0.0);
    pid->out = pid->proportional + pid->integrator + pid->differentiator;
    if (pid->out > pid->limMax)
    {
        pid->out = pid->limMax;
    }
    else if (pid->out < pid->limMin)
    {
        pid->out = pid->limMin;
    }
    pid->prevError = error;
    pid->prevMeasurement = _IQtoIQ15(measurement);
    return _IQ15toIQ(pid->out);
}

/*** PID ***/
/***********************************************************************************************************************************************/

/***********************************************************************************************************************************************/
/*** lowpass filter ***/

filter_typedef *filter_new(void)
{
    return (filter_typedef *)calloc(1, sizeof(filter_typedef));
}

void filter_init(filter_typedef *handle, _iq cutoff_freq, _iq sample_time)
{

    _iq rc = _IQdiv(_IQ(1.0), _IQmpy(_IQ(_2PI), cutoff_freq));
    handle->k[0] = _IQdiv(sample_time, sample_time + rc);
    handle->k[1] = _IQdiv(rc, sample_time + rc);

    //    handle->k[0] = _IQ(0.1);
    //    handle->k[1] = _IQ(0.9);

    handle->output[0] = _IQ(0.0);
    handle->output[1] = _IQ(0.0);
}

_iq filter_update(filter_typedef *handle, _iq input)
{

    handle->output[1] = handle->output[0];
    handle->output[0] = _IQmpy(handle->k[0], input) + _IQmpy(handle->k[1], handle->output[1]);

    return handle->output[0];
}

/*** lowpass filter ***/
/***********************************************************************************************************************************************/

/***********************************************************************************************************************************************/
/*** state & config ***/

config_typedef *config_new(void)
{

    return (config_typedef *)calloc(1, sizeof(config_typedef));
}
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

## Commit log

2022-10-30 fix: add comment to kernal code.
    [main.c]
2022-11-06 feat:添加通讯协议实现层函数
2023-01-20 # This is a combination of 39 commits. # This is the 1st commit message:
    feat: add foc_v2_software, complete open loop control.
    # This is the commit message #2:
    feat: add as5600 read angle, by i2c fast mode!
    # This is the commit message #3:
    feat: add open-loop svpwm and timer.
    # This is the commit message #4:
    fix: prepare for iqmath.
    # This is the commit message #5:
    fix: add IQmath code and update foc_kernal.c
    # This is the commit message #6:
    feat: add DMA in adc!
    # This is the commit message #7:
    feat: add icon
    # This is the commit message #8:
    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
    [GIA_总装配.SLDASM, motor_default_settings.csv, 偏心轴.SLDPRT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]
2023-01-20 feat: add foc_v2_software, complete open loop control.
    feat: add test
    feat: prepare for architech software.
    feat:
    1. lowpass filter demo
    2. encoder demo
    3. foc demo
    4. current sample demo
    5. pid demo
    6. use typedef
    feat: add can filter demo.
    feat: add convert function
    doc: update stm32 doc.
    feat: complete can communication and basic protocol
    feat: 添加了电流环闭环测试，50HZ正弦测试通过
    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
    [motor_default_settings.csv, pid_cur.csv, pid_vel.csv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]
2023-01-28 doc: 添加SDO/PDO默认值.
    [SDO_PDO默认值.xlsx]

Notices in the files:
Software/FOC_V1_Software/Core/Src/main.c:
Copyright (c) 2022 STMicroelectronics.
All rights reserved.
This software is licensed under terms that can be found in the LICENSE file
